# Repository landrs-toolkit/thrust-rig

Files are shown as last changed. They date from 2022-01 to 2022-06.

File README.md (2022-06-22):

# THRUST RIG
The Thrust Rig is used to test the thrust from different motor propeller combinations.

## Hardware Required
i)   HX711 Weight Sensor Module

ii)  5Kg Load Cell

iii) Raspberry Pi

iv)  Brushless DC Motor

v)   Propellers

vi)  Electronic Speed Controllers

vii) Push Button

## Assembling the hardware
### Connecting the HX711 Weight Sensor Module to Raspberry Pi
i)    VCC to Raspberry Pi Pin 2 (5V)
 
ii)   GND to Raspberry Pi Pin 6 (GND)

iii)  DT to Raspberry Pi Pin 29 (GPIO 5)

iv)   SCK to Raspberry Pi Pin 31 (GPIO 6)

### Connecting the ESC to the Raspberry Pi
Note: Do not connect the 5v pin to the Raspberry PI
i) Black pin to GND

ii) Yellow Pin to Pi Pin 7 (GPIO 4)

### Connecting the ESC to the Motor

## Connecting to raspberry pi via shh

### Installing raspberry pi imager

i)    visit https://www.raspberrypi.org/downloads 

ii)   Download the Raspberry Pi Imager installer for your Operating System and run installer

iii)  Launch Raspberry Pi Imager and choose raspberry pi OS

iv)   click the settings(advanced options) icon and to the following- enable ssh,set username or password for the pi, (in our case password is "drone" but    can be customized,configure wireless LAN (network youll be connecting your pi to)the ssid and password must match your wireless network and click save.

v)   choose SD CARD under storage & click write

### ssh into raspberry pi

i)    make sure your computer and raspberry are connected to the same network

ii)   in command line use the command below to reach your raspberry via ssh
```bash
ssh pi@raspberrypi.local
```
iii) when prompted for password enter password you setup initially in the pi imager (in this case my password is "drone")

iv) voila you're have successfully got into the raspberry pi :).

## Running the files
Clone the repository using the command below
```bash
$git clone https://github.com/RogeK/Thrust_Rig.git
```

Navigate to the src directory

The mass of the motor and the propeller may affect the accuracy of your reading. To prevent this, run the example.py file and press the push button. The value of the readings will be set to 0.

To run the example.py file, run the command below
```bash
python3 example.py
```
Once the value of the readings have been set to 0, exit the program by pressing ctrl + c keys. You can now start testing the thrust of the motor by running the command below

```bash
python3 start.py
```
The thrust values are written to the Thrust_Values.csv file in the src directory

## License
[MIT](https://choosealicense.com/licenses/mit/)

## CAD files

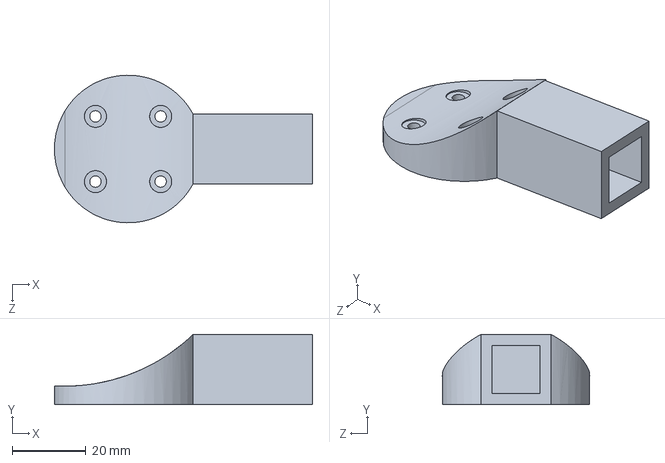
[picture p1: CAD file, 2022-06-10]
Mechanical Design/SolidWorks Files/TMotor-MN5008-MountV1.0.SLDPRT
69.9 x 19.0 x 40.0 mm

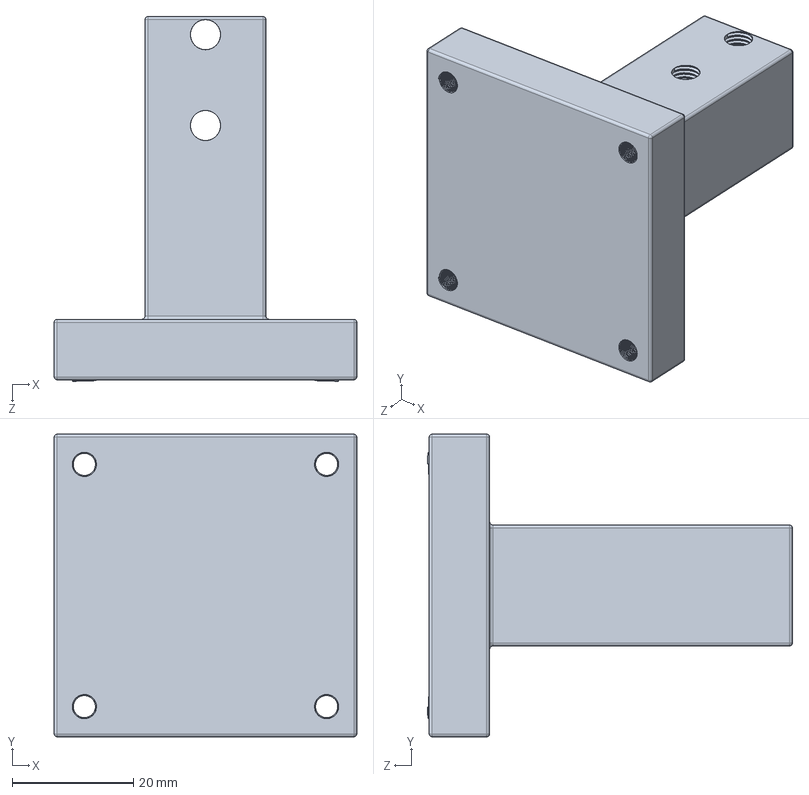
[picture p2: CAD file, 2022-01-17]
Mechanical Design/SolidWorks Files/Stand.SLDPRT
50.0 x 50.0 x 60.3 mm

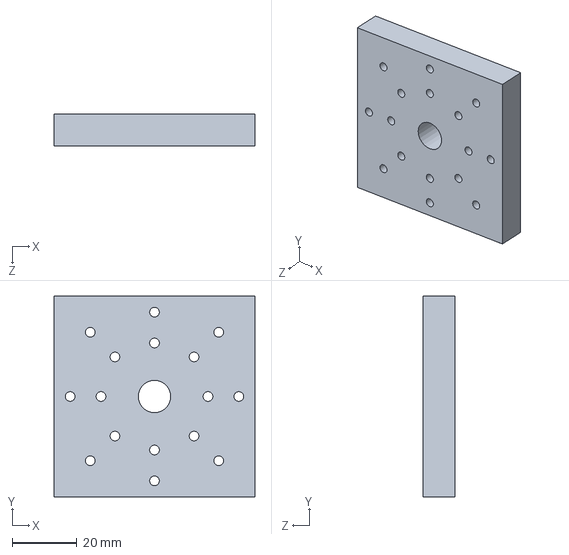
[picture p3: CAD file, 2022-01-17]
Mechanical Design/SolidWorks Files/Expansion.SLDPRT
62.0 x 62.0 x 10.0 mm

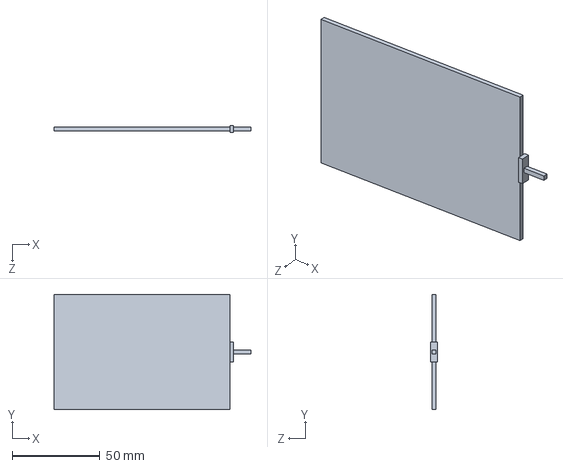
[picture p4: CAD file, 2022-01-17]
Mechanical Design/SolidWorks Files/Pi_Lid.SLDPRT
112.0 x 65.6 x 3.97 mm

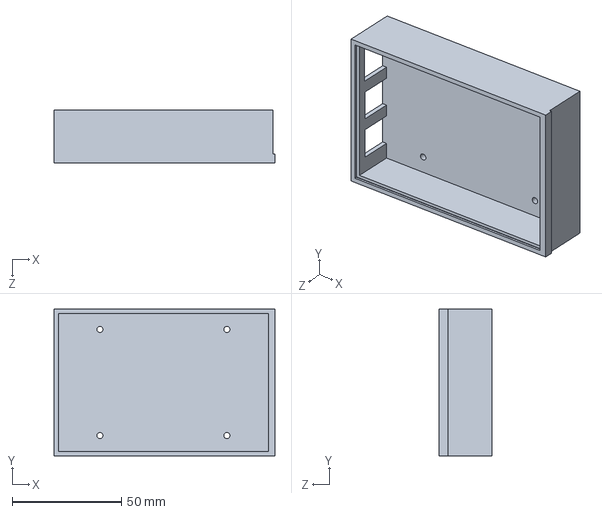
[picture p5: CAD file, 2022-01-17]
Mechanical Design/SolidWorks Files/Pi_Case.SLDPRT
101.0 x 67.0 x 24.0 mm

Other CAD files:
Mechanical Design/STL Files/Expansion.STL
Mechanical Design/STL Files/Pi_Case.STL
Mechanical Design/STL Files/Pi_Lid.STL

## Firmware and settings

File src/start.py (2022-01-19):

#! /usr/bin/python2

from time import sleep
import pigpio
import datetime
import RPi.GPIO as GPIO
import sys
import csv

EMULATE_HX711=False

#referenceUnit = 1
referenceUnit = 2253
GPIO.setwarnings(False)


if not EMULATE_HX711:
    import RPi.GPIO as GPIO
    from hx711 import HX711
    print("Another hx711")
else:
    from emulated_hx711 import HX711

def cleanAndExit():
    print("Cleaning...")

    if not EMULATE_HX711:
        GPIO.cleanup()
        print("Just hx711")
    print("Bye!")
    sys.exit()

hx = HX711(5, 6)
push_button = 18
LED_Light = 23
GPIO.setmode(GPIO.BCM)
GPIO.setup(push_button, GPIO.IN)
GPIO.setup(push_button, GPIO.IN, pull_up_down=GPIO.PUD_UP)
GPIO.setup(LED_Light, GPIO.OUT)
pi = pigpio.pi()


def Turn_LED_ON():
    if GPIO.input(push_button):
        sleep(0.25)
        if GPIO.input(push_button):
            hx.tare()
            GPIO.output(LED_Light,GPIO.LOW)
    else:
        GPIO.output(LED_Light, GPIO.HIGH)
    pass

hx.set_reading_format("MSB", "MSB")
hx.set_reference_unit(referenceUnit)
hx.reset()
hx.tare()
print("Tare done! Add weight now...")
Tvals = []
buses = []
i=0
print("Calibrating the ESC\n")
Max_Value = input("Enter the Max Throttle value\n")
Min_Value = input("Enter the Min Throttle value\n")

Max_Value = int(Max_Value)
Min_Value = int(Min_Value)

ESC_GPIO = 4
#pi.set_servo_pulsewidth(ESC_GPIO,Max_Value) #Max Throttle
pi.set_servo_pulsewidth(ESC_GPIO,Max_Value)
sleep(5)
#pi.set_servo_pulsewidth(ESC_GPIO,Min_Value) #Min Throttle
pi.set_servo_pulsewidth(ESC_GPIO,Min_Value)
sleep(5)
speed = Min_Value
print("Speed of motor will now increase from Min to Max Throttle")
sleep(1)


#pi.set_servo_pulsewidth(ESC_GPIO,speed)

while True:
    try:
        if(GPIO.input(push_button)):
            sleep(0.25)
            if(GPIO.input(push_button)):
                GPIO.output(LED_Light,GPIO.HIGH)
        else:
            GPIO.output(LED_Light,GPIO.LOW)
            hx.tare()
        while(speed<1900):
            pi.set_servo_pulsewidth(ESC_GPIO,speed)
            #speed+=100
            sleep(5)
            print(speed)
            for j in range(10):
                val = hx.get_weight(5)
                val = round(val,0)
                Tvals.append(val)
                print(val)
                buses.append(i)
                i=i+1
            speed+=100
        val = hx.get_weight(5)
        val = round(val,0)
        Tvals.append(val)
        print(val)
        buses.append(i)
        i=i+1
        hx.power_down()
        hx.power_up()
        sleep(0.1)
    except(KeyboardInterrupt, SystemExit):
        speed = 0
        now = datetime.datetime.now()
        pi.set_servo_pulsewidth(ESC_GPIO,0)
        pi.stop()
        print("Motor has stopped\n")
        print("Done_Completely")
        file = open("Thrust_Values.csv", "a", encoding='UTF8', newline='')
        writer = csv.writer(file)
        writer.writerow(now.strftime("%Y-%m-%d %H:%M:%S"))
        for w in range(len(buses)):
            writer.writerow([buses[w], Tvals[w]])
        file.close()
        cleanAndExit()

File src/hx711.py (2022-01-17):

#
import RPi.GPIO as GPIO
import time
import threading
import csv

Vvalues = [1,2,3]
class HX711:

    def __init__(self, dout, pd_sck, gain=128):
        self.PD_SCK = pd_sck

        self.DOUT = dout

        # Mutex for reading from the HX711, in case multiple threads in client
        # software try to access get values from the class at the same time.
        self.readLock = threading.Lock()

        push_button = 18
        LED_Light = 23
        GPIO.setmode(GPIO.BCM)
        GPIO.setup(push_button, GPIO.IN)
        GPIO.setup(push_button, GPIO.IN, pull_up_down=GPIO.PUD_UP)
        GPIO.setup(LED_Light, GPIO.OUT)
        GPIO.setup(self.PD_SCK, GPIO.OUT)
        GPIO.setup(self.DOUT, GPIO.IN)

        self.GAIN = 0
        # The value returned by the hx711 that corresponds to your reference
        # unit AFTER dividing by the SCALE.
        self.REFERENCE_UNIT = 1
        self.REFERENCE_UNIT_B = 1

        self.OFFSET = 1
        self.OFFSET_B = 1
        self.lastVal = int(0)

        self.DEBUG_PRINTING = False

        self.byte_format = 'MSB'
        self.bit_format = 'MSB'

        self.set_gain(gain)

        # Think about whether this is necessary.
        time.sleep(1)


    def convertFromTwosComplement24bit(self, inputValue):
        return -(inputValue & 0x800000) + (inputValue & 0x7fffff)


    def is_ready(self):
        return GPIO.input(self.DOUT) == 0
    
    def set_gain(self, gain):
        if gain is 128:
            self.GAIN = 1
        elif gain is 64:
            self.GAIN = 3
        elif gain is 32:
            self.GAIN = 2

        GPIO.output(self.PD_SCK, False)

        # Read out a set of raw bytes and throw it away.
        self.readRawBytes()

    def get_gain(self):
        if self.GAIN == 1:
            return 128
        if self.GAIN == 3:
            return 64
        if self.GAIN == 2:
            return 32

        # Shouldn't get here.
        return 0


    def readNextBit(self):
       # Clock HX711 Digital Serial Clock (PD_SCK).  DOUT will be
       # ready 1us after PD_SCK rising edge, so we sample after
       # lowering PD_SCL, when we know DOUT will be stable.
       GPIO.output(self.PD_SCK, True)
       GPIO.output(self.PD_SCK, False)
       value = GPIO.input(self.DOUT)

       # Convert Boolean to int and return it.
       return int(value)

    def readNextByte(self):
       byteValue = 0

       # Read bits and build the byte from top, or bottom, depending
       # on whether we are in MSB or LSB bit mode.
       for x in range(8):
          if self.bit_format == 'MSB':
             byteValue <<= 1
             byteValue |= self.readNextBit()
          else:
             byteValue >>= 1
             byteValue |= self.readNextBit() * 0x80

       # Return the packed byte.
       return byteValue

    def readRawBytes(self):
        # Wait for and get the Read Lock, incase another thread is already
        # driving the HX711 serial interface.
        self.readLock.acquire()

        # Wait until HX711 is ready for us to read a sample.
        while not self.is_ready():
           pass

        # Read three bytes of data from the HX711.
        firstByte  = self.readNextByte()
        secondByte = self.readNextByte()
        thirdByte  = self.readNextByte()

        # HX711 Channel and gain factor are set by number of bits read
        # after 24 data bits.
        for i in range(self.GAIN):
           # Clock a bit out of the HX711 and throw it away.
           self.readNextBit()
        # Release the Read Lock, now that we've finished driving the HX711
        # serial interface.
        self.readLock.release()

        # Depending on how we're configured, return an orderd list of raw byte
        # values.
        if self.byte_format == 'LSB':
           return [thirdByte, secondByte, firstByte]
        else:
           return [firstByte, secondByte, thirdByte]

    def read_long(self):
        # Get a sample from the HX711 in the form of raw bytes.
        dataBytes = self.readRawBytes()


        if self.DEBUG_PRINTING:
            print(dataBytes,)

        # Join the raw bytes into a single 24bit 2s complement value.
        twosComplementValue = ((dataBytes[0] << 16) |
                               (dataBytes[1] << 8)  |
                               dataBytes[2])

        if self.DEBUG_PRINTING:
            print("Twos: 0x%06x" % twosComplementValue)

        # Convert from 24bit twos-complement to a signed value.
        signedIntValue = self.convertFromTwosComplement24bit(twosComplementValue)

        # Record the latest sample value we've read.
        self.lastVal = signedIntValue

        # Return the sample value we've read from the HX711.
        return int(signedIntValue)

    def read_average(self, times=3):
        # Make sure we've been asked to take a rational amount of samples.
        if times <= 0:
            raise ValueError("HX711()::read_average(): times must >= 1!!")

        # If we're only average across one value, just read it and return it.
        if times == 1:
            return self.read_long()

        # If we're averaging across a low amount of values, just take the
        # median.
        if times < 5:
            return self.read_median(times)

        # If we're taking a lot of samples, we'll collect them in a list, remove
        # the outliers, then take the mean of the remaining set.
        valueList = []

        for x in range(times):
            valueList += [self.read_long()]

        valueList.sort()

        # We'll be trimming 20% of outlier samples from top and bottom of collect$
        trimAmount = int(len(valueList) * 0.2)

        # Trim the edge case values.
        valueList = valueList[trimAmount:-trimAmount]

        # Return the mean of remaining samples.
        return sum(valueList) / len(valueList)

    # A median-based read method, might help when getting random value spikes
    # for unknown or CPU-related reasons
    def read_median(self, times=3):
       if times <= 0:
          raise ValueError("HX711::read_median(): times must be greater than zero!")


       # If times == 1, just return a single reading.
       if times == 1:
          return self.read_long()

       valueList = []

       for x in range(times):
          valueList += [self.read_long()]

       valueList.sort()

       # If times is odd we can just take the centre value.
       if (times & 0x1) == 0x1:
          return valueList[len(valueList) // 2]
       else:
          # If times is even we have to take the arithmetic mean of
          # the two middle values.
          midpoint = len(valueList) / 2
          return sum(valueList[midpoint:midpoint+2]) / 2.0

    # Compatibility function, uses channel A version
    def get_value(self, times=3):
        return self.get_value_A(times)


    def get_value_A(self, times=3):
        return self.read_median(times) - self.get_offset_A()
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

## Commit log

2022-01-17 Add files via upload
    Merged Motor.py with hx711.py
2022-01-17 Changed name of csv file to Thrust_Values.csv
2022-01-17 Add files via upload
    Solidworks and STL Files
    [Expansion.SLDPRT, Expansion.STL, Pi_Case.SLDPRT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]
2022-01-19 Added HX711 wiring connection to RPi
2022-01-19 Added wiring instructions for ESC to Rpi
2022-06-10 Update: Soldiworks file V1 of Tmotor MN5008 thrust rig mount
    [TMotor-MN5008-MountV1.0.SLDPRT]
2022-06-22 Update README.md
    added instructions on how to connect to raspberry pi via ssh
